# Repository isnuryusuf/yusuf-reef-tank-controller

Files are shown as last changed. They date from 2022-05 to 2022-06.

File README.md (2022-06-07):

# MrAqua Aquarium Controller

This project was based off the iAqua controller written by Dan Cunningham with new features and updates here.

Controller home screen

## Features

- Water temperature monitoring
  - Allows calibration
  - Automatic shutoff of heater if water exceeds setpoint
- Automatic water top-off 
  - Float switch inputs for tank and reservoir
  - Set maximum run-time with alarm flagged if exceeded
  - using non touch water sensor
- Feeding mode
  - Monitor time since last fed
  - Control outlets during feeding (ie turn off pumps)
- Light control 
  - 6-channel PWM or IR control of e-series LED
  - 4 lighting levels (moonlight, sunrise, mid-morning and full daylight)
- Dosing
  - 8 channels
  - Individual settings for each channel
- 8 power outlet control
  - Manual control or set on/off times
  - Aux outlets can be set to cycle times (ie on 10 minutes every 2 hours)
- Buzzer for allerting

## Hardware

- Arduino Mega
- 320 x 240 LCD
- Arduino Mega TFT Shield (or custom shield below)
- 12V power supply
- 8 channel relay board
- DS18B20 temperature sensor
- Peristaltic pumps
- Float switch
- Submersible 12V pump
- (Optional)PCA9685 breakout board

## Libraries

- [Adafruit PWM Servo Driver](https://github.com/adafruit/Adafruit-PWM-Servo-Driver-Library)
- [Dallas Temperature](https://github.com/milesburton/Arduino-Temperature-Control-Library)
- [Time Library](https://github.com/PaulStoffregen/Time)
- [Arduino IR Remote](https://github.com/z3t0/Arduino-IRremote)
- [DS1307RTC](https://github.com/PaulStoffregen/DS1307RTC)
- [SdFat](https://github.com/greiman/SdFat)
- [TimeAlarms](https://github.com/PaulStoffregen/TimeAlarms)
- [UTFT](http://www.rinkydinkelectronics.com/library.php?id=51)
- [UTFT_SdRaw](https://platformio.org/lib/show/565/UTFT_SdRaw)
- [URTouch](http://www.rinkydinkelectronics.com/library.php?id=92)

## Setup

If you are using an ecoxotic e-series LED set "lightCSP" to true, otherwise set it to false.  If you are using a PCA9685 chip for PWM set boolean "PCA9685Installed" to true.

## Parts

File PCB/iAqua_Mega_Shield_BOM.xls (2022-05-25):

Designator | DK# | part_value | Quantity
IR1 |  | IR Transmitter | 1
U1 |  | Mega 2560 | 1
U2, U3, U4, U5, U6 | 296-26482-5-ND | 74HC541PW | 5
U12, U13 | 296-27172-1-ND | ULN2003ANSR | 2 | ULN2003AN | 6
C8, C13 | 311-1458-1-ND | 1u | 2
C12, C14 | 399-6098-ND | 47u | 2 | ELKO Kapasitor 47UF 50V 47UF/50V |  | 8
Q3 (Ambient Light sensor) | 475-1437-ND | SFH 300-3/4 | 1 | TEMT6000
C7 | 490-1799-1-ND | 2u2 | 1
U8 | 497-7253-1-ND | L7805ACD2T-TR | 1
U10 | 497-14661-1-ND | LDF33DT-TR | 1
U9 | 568-8366-5-ND | PCA9685 | 1
ATO, Fan1, Fan2, FloatSwitch1, FloatSwitch2, J2, Pump1, Pump2, Pump3 | 609-3918-ND | 2Pin Terminal Block | 9
P3, P4 | 609-3926-ND | 10Pin Terminal Block | 2
C1, C2, C3, C4, C5, C6, C9, C11 | 1276-1003-1-ND | 100n | 8
C10 | 1276-1123-1-ND | 330n | 1
B1 | 3001K-ND | 3001 | 1
D1, D7 | B340A-FDICT-ND | B340A-13-F | 2
Q4 | DMN3032LE-13DICT-ND | DMN3032LE-13 | 1
U7 | DS1307Z+T&RCT-ND | DS1307 | 1 | DS1307
U11 | MCP9701AT-E/TTCT-ND | MCP9701AT-E/TT | 1 | MCP9700 |  |  | ds18b20
Q1 | MMBT2222AFSCT-ND | MMBT2222A | 1 | Transistor S8050 NPN 0.5A 40V | 4
Q2 | MMBT2907AFSCT-ND | MMBT2907A | 1 | Transistor PN 4355 PN4355
R9, R10, R20, R22, R32, R33 | P1.0KACT-ND | 1K0 | 6
R1, R11 | P4.7KACT-ND | 4K7 | 2
R21 | P10ACT-ND | 10R0 | 1
R4, R5, R12, R13, R14, R15, R16, R24, R30, R34 | P10KACT-ND | 10K0 | 10
R2, R3, R28, R35, R36, R37, R38, R39, R40 | P100ACT-ND | 100R | 9
R27 | P100KACT-ND | 100K | 1
R23 | P499CCT-ND | 499R | 1 | Vishay Dale Resistor 499 Ohm RN60 Series | 6
JP1 | S1011EC-03-ND | 3pin header | 1
P1, P2 | S1011EC-03-ND | 3pin header | 2
P10 (Pin Header Connector) | S1011EC-10-ND | 10Pin Header | 1
HD1, HS1, HS2 (Pin Header Connector) | S2012EC-18-ND, A113648-ND | 38 pin header, 40 pin single row header | 3
P9 (Board Mount Connectors) | S6104-ND | PRPC020DAAN-RC | 1
Y1 | X1123-ND | ECS-3X8X | 1

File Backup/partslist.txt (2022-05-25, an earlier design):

Partlist

Exported from iAqua shield.brd at 12/9/2014 10:39:06 PM

EAGLE Version 6.4.0 Copyright (c) 1988-2013 CadSoft

Assembly variant: 

Part     Value            Package                   Library                    Position (mm)         Orientation

BAT1     3.3V             BATTCON_12MM              SparkFun-Electromechanical (41.46401875 44.49636875) MR90
C1       470pf            C1206                     resistor                   (81.0571875 12.8081)  R0
C2       10uf             C1206                     resistor                   (15.01819375 56.92936875) R0
C3       10uf             C1206                     resistor                   (13.620215625 44.933665625) R270
C4       10uf             C1206                     resistor                   (13.5467375 32.13441875) R270
D1       CGRM4007-G       SOD-123_MINI-SMA          diode                      (32.084071875 75.29981875) R270
D2       CGRM4007-G       SOD-123_MINI-SMA          diode                      (37.9979125 75.186)   R270
D3       CGRM4007-G       SOD-123_MINI-SMA          diode                      (44.097415625 75.182) R270
D4       CGRM4007-G       SOD-123_MINI-SMA          diode                      (50.159846875 75.18935625) R270
D5       CGRM4001-G       SOD-123_MINI-SMA          diode                      (13.080740625 80.4300125) R0
D6       CGRM4001-G       SOD-123_MINI-SMA          diode                      (20.58725 80.4871)    R0
D7       CGRM4001-G       SOD-123_MINI-SMA          diode                      (13.504265625 38.09000625) R270
D8       CGRM4001-G       SOD-123_MINI-SMA          diode                      (13.590159375 52.011784375) R270
IC1      UA7812           TO263-3                   linear                     (22.99915 51.5953875) R270
IC2      UA7805           TO263-3                   linear                     (23.000540625 37.37434375) R270
J1       POWER_JACKPTH    POWER_JACK_PTH            SparkFun-Connectors        (-2.762478125 13.4475875) R270
JP1                       1X01                      pinhead                    (39.3623875 57.384965625) R0
JP2                       1X03                      pinhead                    (85.601328125 5.52231875) R270
JP3                       1X03                      pinhead                    (78.409140625 5.523759375) R90
JP4                       1X04                      pinhead                    (77.156325 78.61265)  R0
JP5                       1X04                      pinhead                    (77.156325 84.2062875) R0
JP6                       1X04                      pinhead                    (77.156321875 89.36450625) R0
JP7                       1X01                      pinhead                    (53.33334375 63.6615375) R0
JP8                       1X01                      pinhead                    (45.70205 63.591934375) R0
JP9                       1X01                      pinhead                    (48.282596875 63.629696875) R0
JP10                      1X01                      pinhead                    (50.815209375 63.653721875) R0
JP11                      1X01                      pinhead                    (18.78530625 62.82380625) R0
JP12                      1X01                      pinhead                    (68.593115625 27.40033125) R0
JP13                      1X01                      pinhead                    (71.142221875 27.383353125) R0
JP14                      1X01                      pinhead                    (78.746009375 27.377815625) R0
JP15                      1X01                      pinhead                    (81.2744375 27.447925) R0
JP16                      1X01                      pinhead                    (73.63146875 27.3715375) R0
JP17                      1X01                      pinhead                    (76.219753125 27.400315625) R0
JP18                      1X01                      pinhead                    (21.316075 62.807553125) R0
LED1     POWER            CHIPLED_1206              led                        (20.334503125 15.73700625) R90
LED2                      LED5MM                    led                        (63.55200625 86.103553125) R180
R1       10K              M1206                     resistor                   (26.472746875 15.75471875) R180
R2       220              M1206                     resistor                   (29.1469 75.711715625) R270
R3       220              M1206                     resistor                   (35.061815625 75.5995625) R270
R4       220              M1206                     resistor                   (41.0167875 75.569996875) R270
R5       220              M1206                     resistor                   (47.19305625 75.58815625) R270
R6       1.8k             M1206                     resistor                   (85.354040625 78.572078125) R180
R7       1.8k             M1206                     resistor                   (85.35463125 84.1430375) R180
R8       220              M1206                     resistor                   (35.9079125 15.438390625) R90
R9       220              M1206                     resistor                   (39.726771875 15.395709375) R90
R10      220              M1206                     resistor                   (43.87718125 15.39609375) R90
R11      220              M1206                     resistor                   (47.6961 15.31066875) R90
R12      220              M1206                     resistor                   (51.847303125 15.310803125) R90
R13      220              M1206                     resistor                   (55.6509875 15.30815) R90
R14      220              M1206                     resistor                   (59.868953125 15.4823) R90
R15      220              M1206                     resistor                   (63.68051875 15.481846875) R90
R31      1K               M1206                     resistor                   (39.126421875 62.447896875) R180
R32      150              M1206                     resistor                   (66.69430625 75.082121875) R180
R33      PHOTOCELLPTH     PHOTOCELL                 SparkFun-Sensors           (71.4802125 8.792246875) R0
R34      100              M1206                     resistor                   (64.80325625 31.58103125) R0
R35      4.7K             M1206                     resistor                   (87.353559375 19.868003125) R180
R36      1K               M1206                     resistor                   (13.55525 75.823171875) R90
R37      1K               M1206                     resistor                   (20.62185 75.475753125) R90
T1                        SOT23-BEC                 transistor                 (45.206290625 58.941078125) R270
T2                        SOT23-BEC                 transistor                 (16.91803125 78.301253125) R0
T3                        SOT23-BEC                 transistor                 (23.96439375 77.9447) R0
U$1      DS1307SO8        SO08                      SparkFun-FreqCtrl          (52.6867 44.71811875) R0
U$2                       1.4CMX1.2CM_HEAT_SINK_PAD Custom Heat Sink           (26.99420625 51.587453125) R0
U$3                       1.4CMX1.2CM_HEAT_SINK_PAD Custom Heat Sink           (26.990246875 37.4647625) R0
U1       ARDUINO-MEGAFULL ARDUINO_MEGA              SparkFun-Boards            (-10.16 17.78)        R0
X1       MKDS1/4-3,81     4POL381                   con-phoenix-381            (45.24549375 86.22636875) R180
X2       MKDS1/2-3,81     2POL381                   con-phoenix-381            (31.799553125 8.8005375) R180
X3       MKDS1/4-3,81     4POL381                   con-phoenix-381            (12.140515625 86.1544375) R0
X4       MKDS1/2-3,81     2POL381                   con-phoenix-381            (39.726053125 8.7846875) R180
X5       MKDS1/2-3,81     2POL381                   con-phoenix-381            (47.69358125 8.7846875) R180
X6       MKDS1/2-3,81     2POL381                   con-phoenix-381            (55.661109375 8.7846875) R180
X7       MKDS1/2-3,81     2POL381                   con-phoenix-381            (63.68655625 8.7846875) R180
X8       MKDS1/2-3,81     2POL381                   con-phoenix-381            (53.097559375 86.224359375) R180
Y1       32.768KHz        TC26H                     SparkFun-FreqCtrl          (51.70250625 38.49364375) R180

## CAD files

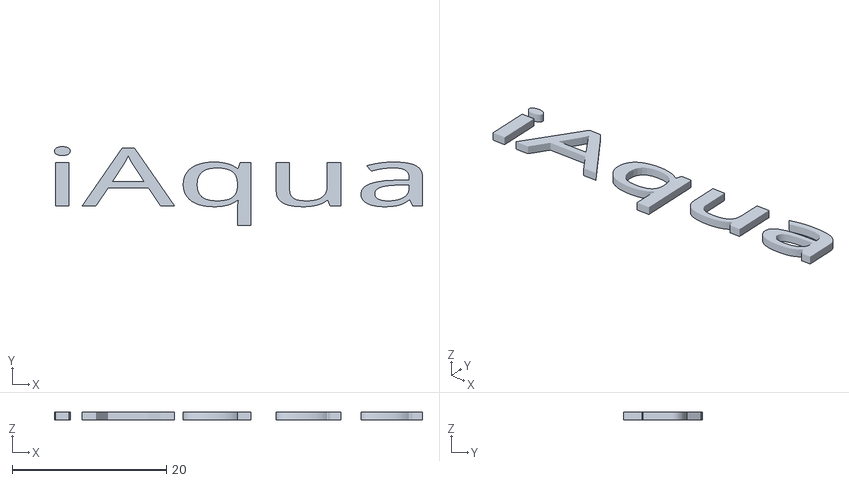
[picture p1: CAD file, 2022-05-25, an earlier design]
Backup/Schrift.stl
47.7 x 10.2 x 1.00

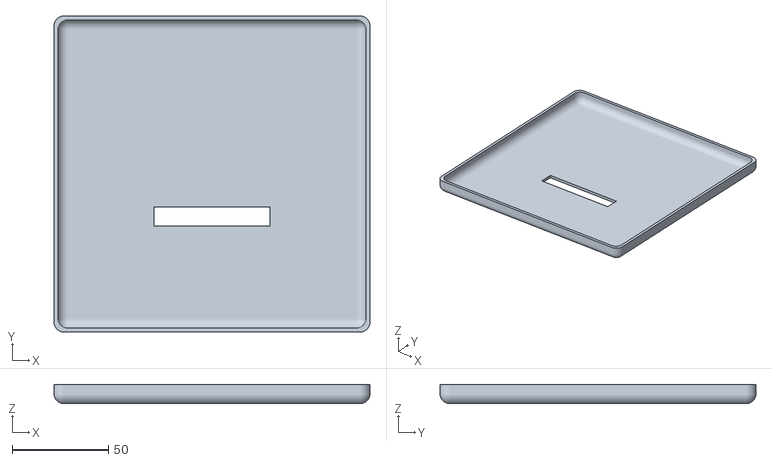
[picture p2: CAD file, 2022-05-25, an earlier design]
Backup/Deckel.stl
164.0 x 164.0 x 10.00

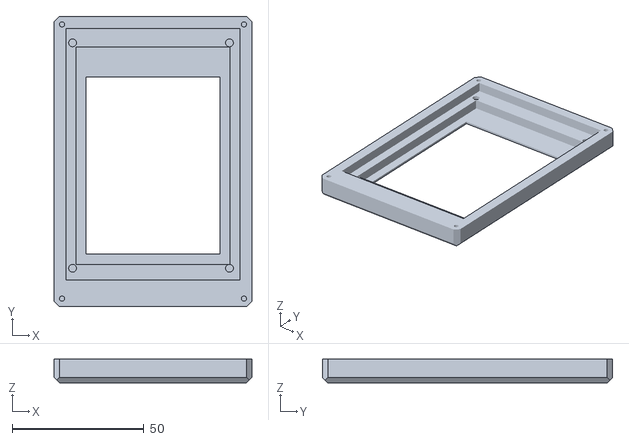
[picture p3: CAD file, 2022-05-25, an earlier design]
Backup/TFT_cover.stl
75.0 x 110.0 x 9.00

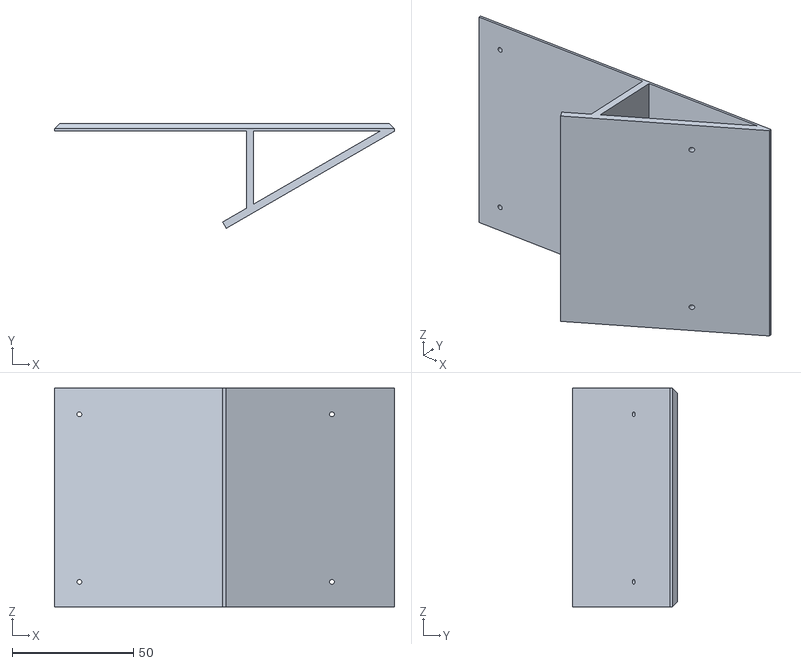
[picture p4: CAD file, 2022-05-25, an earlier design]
Backup/Staender.stl
140.0 x 43.1 x 90.0

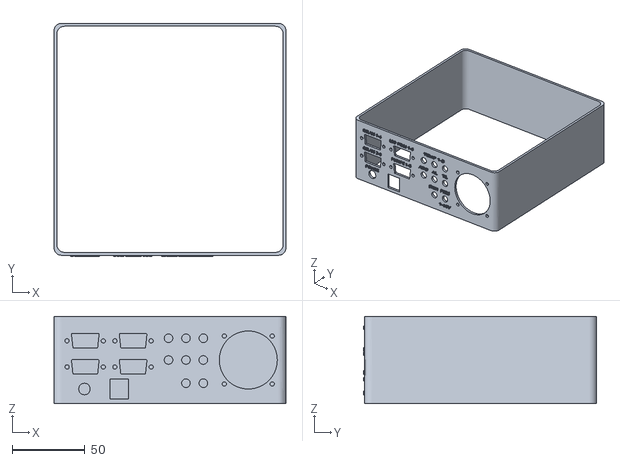
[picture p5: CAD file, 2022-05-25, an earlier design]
Backup/Mittelteil.stl
160.0 x 161.0 x 60.0

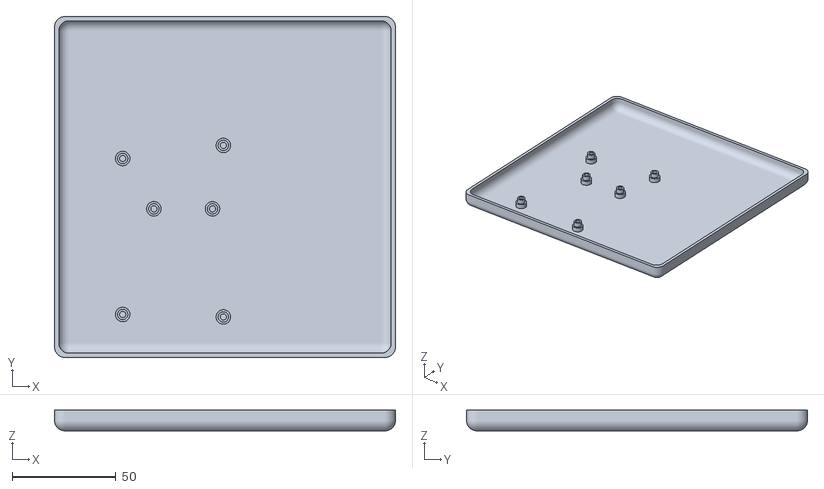
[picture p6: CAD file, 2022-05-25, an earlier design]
Backup/Unterteil.stl
164.0 x 164.0 x 10.00

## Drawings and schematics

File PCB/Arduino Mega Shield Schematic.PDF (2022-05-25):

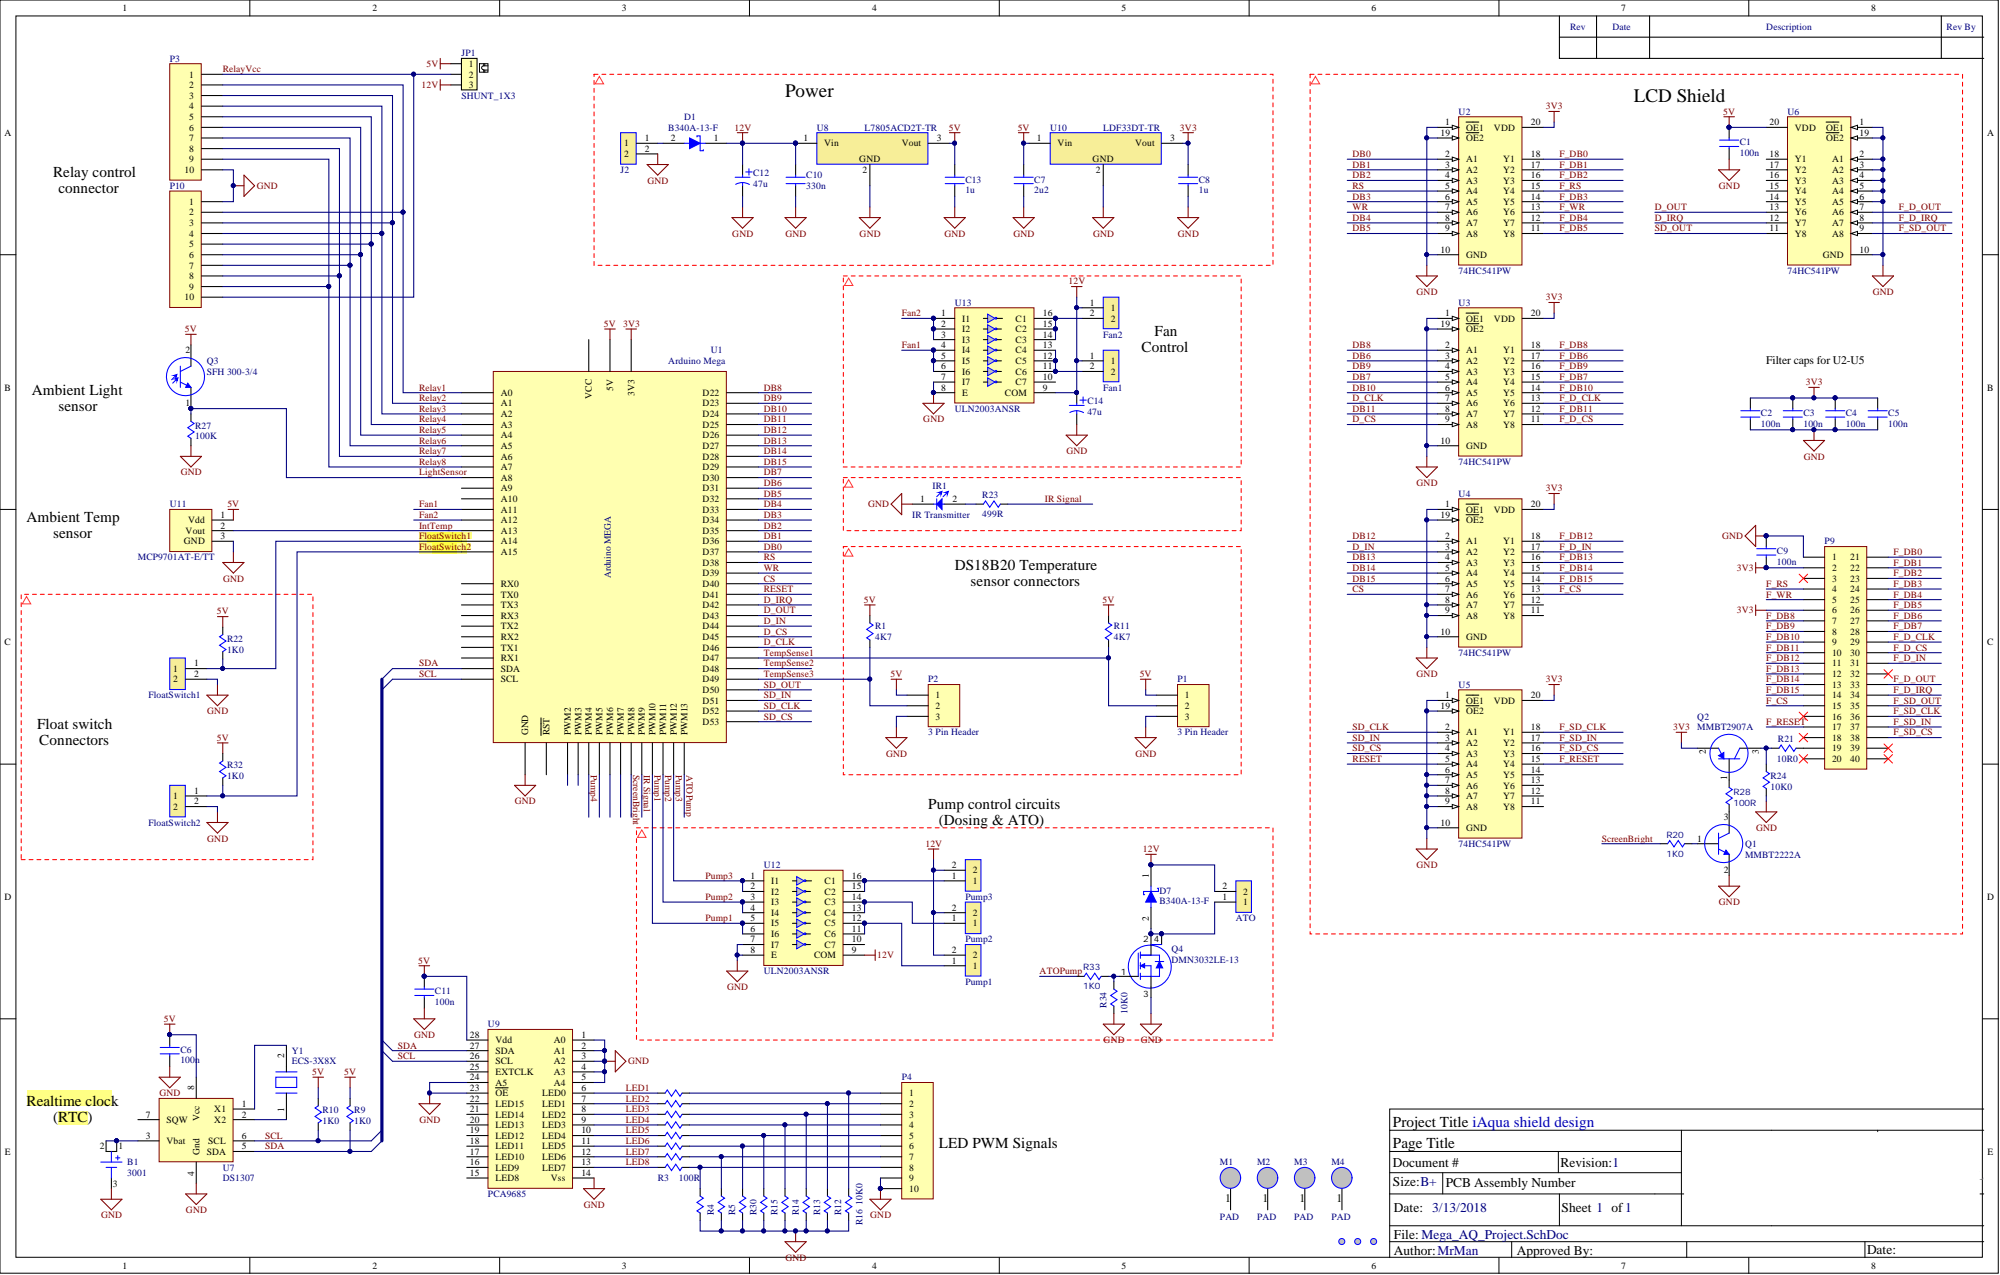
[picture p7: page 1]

2 | D R3 2 | SCL

Page Title | Del ta-Q Technologies Corp. 3755 Wi l l ingdon Bri t ish Columbi | Ave Burnaby a Canada, V5G 3H3 | CO NFIDENTIA PROPRIETARY

# | Revision: 1
B+ | PCB Assembly Number
Date: 3/13/2018 | Sheet 1 of 1 | The information contained in this dr awing is the sole prope rty of Delta -Q T e chnologie s Corp. Any r eproduction in whole or in pa rt without the written pe rmis sion of Delta -Q T e chnologie s Corp. is prohibite d

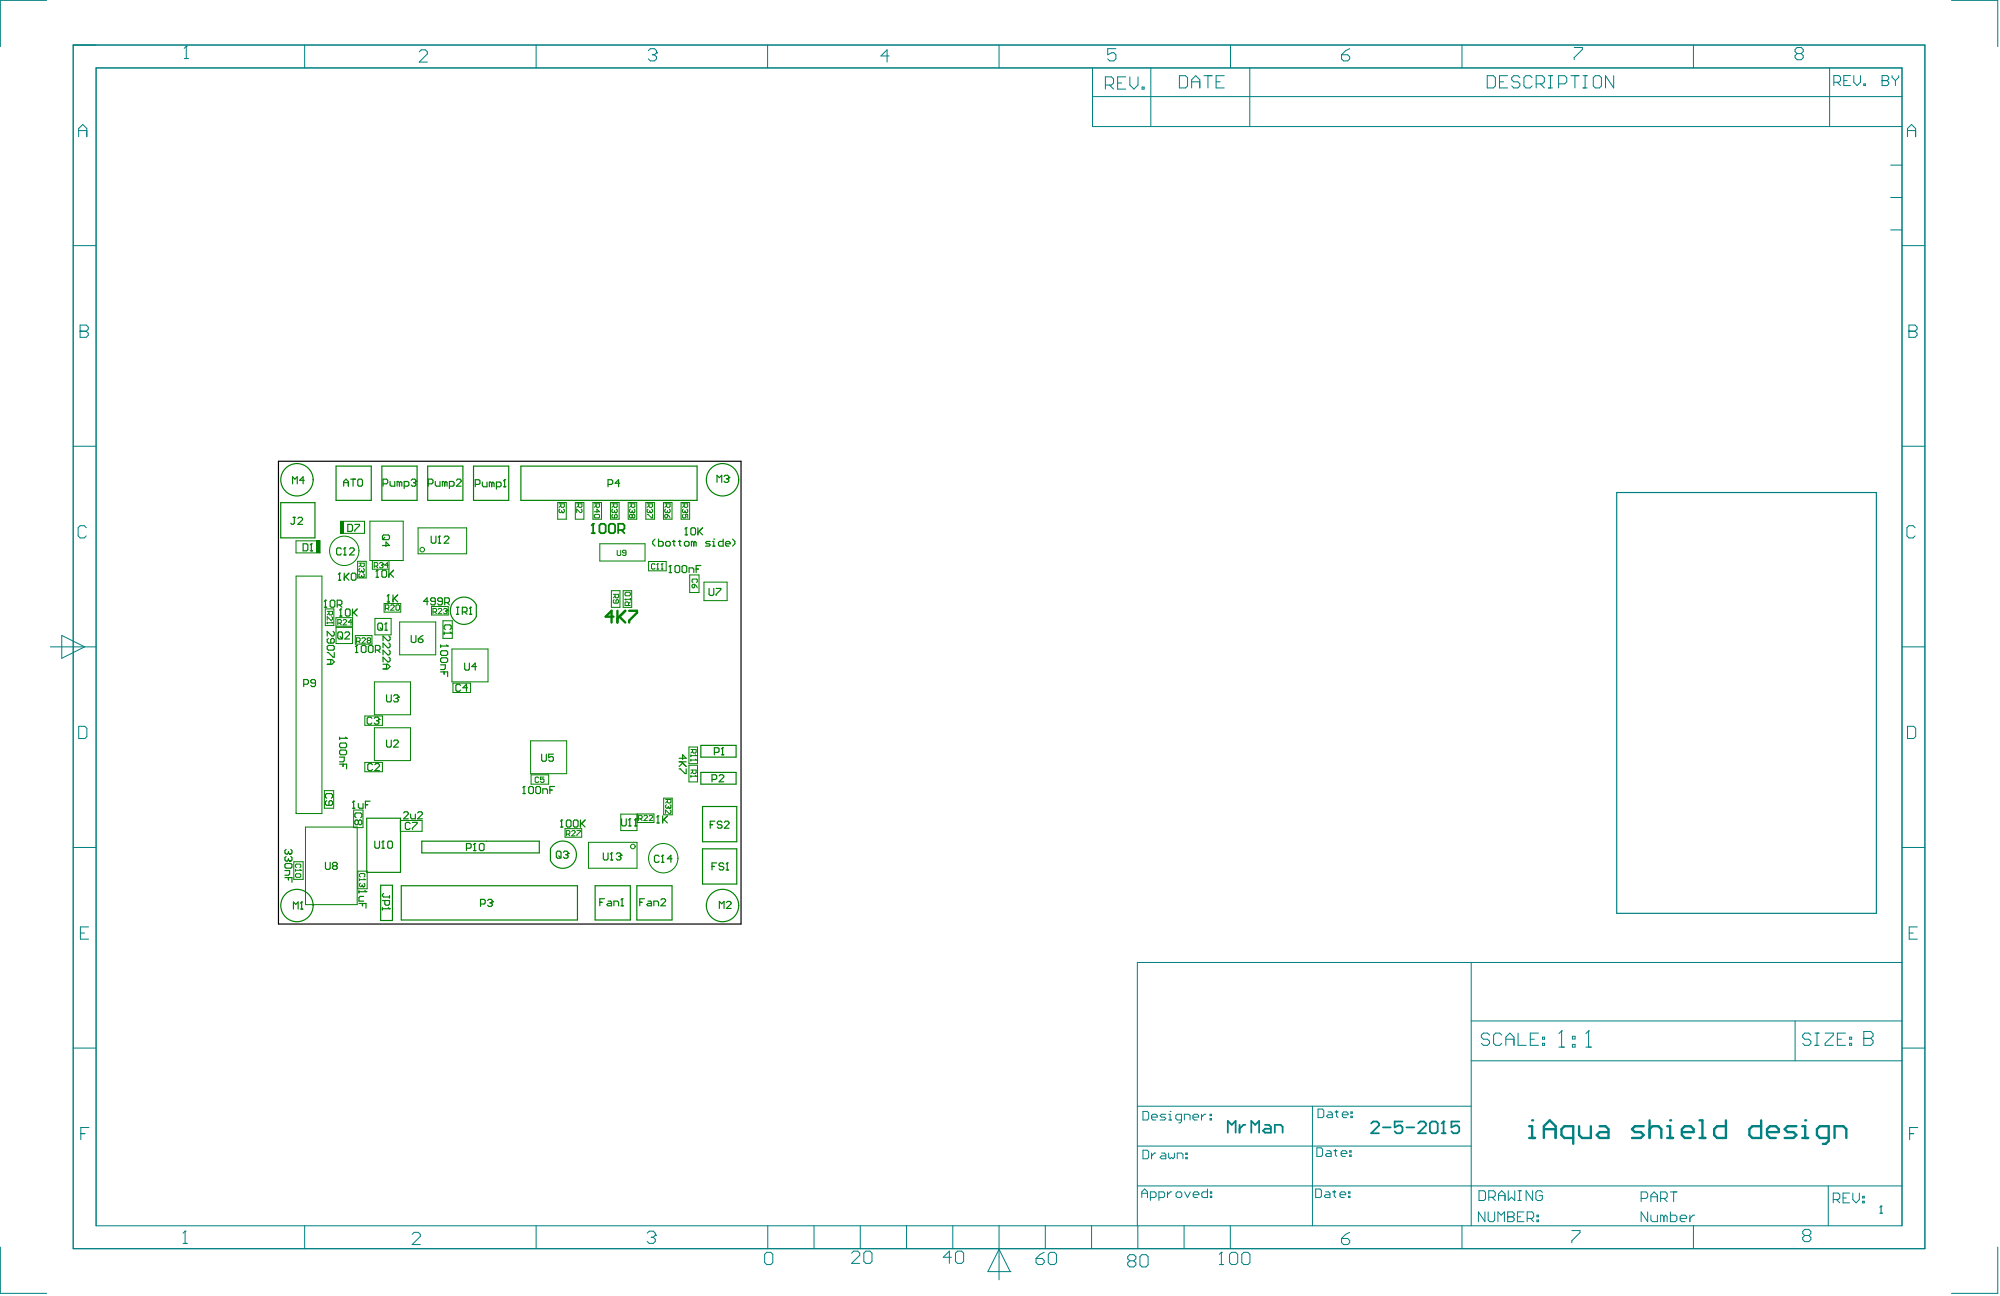
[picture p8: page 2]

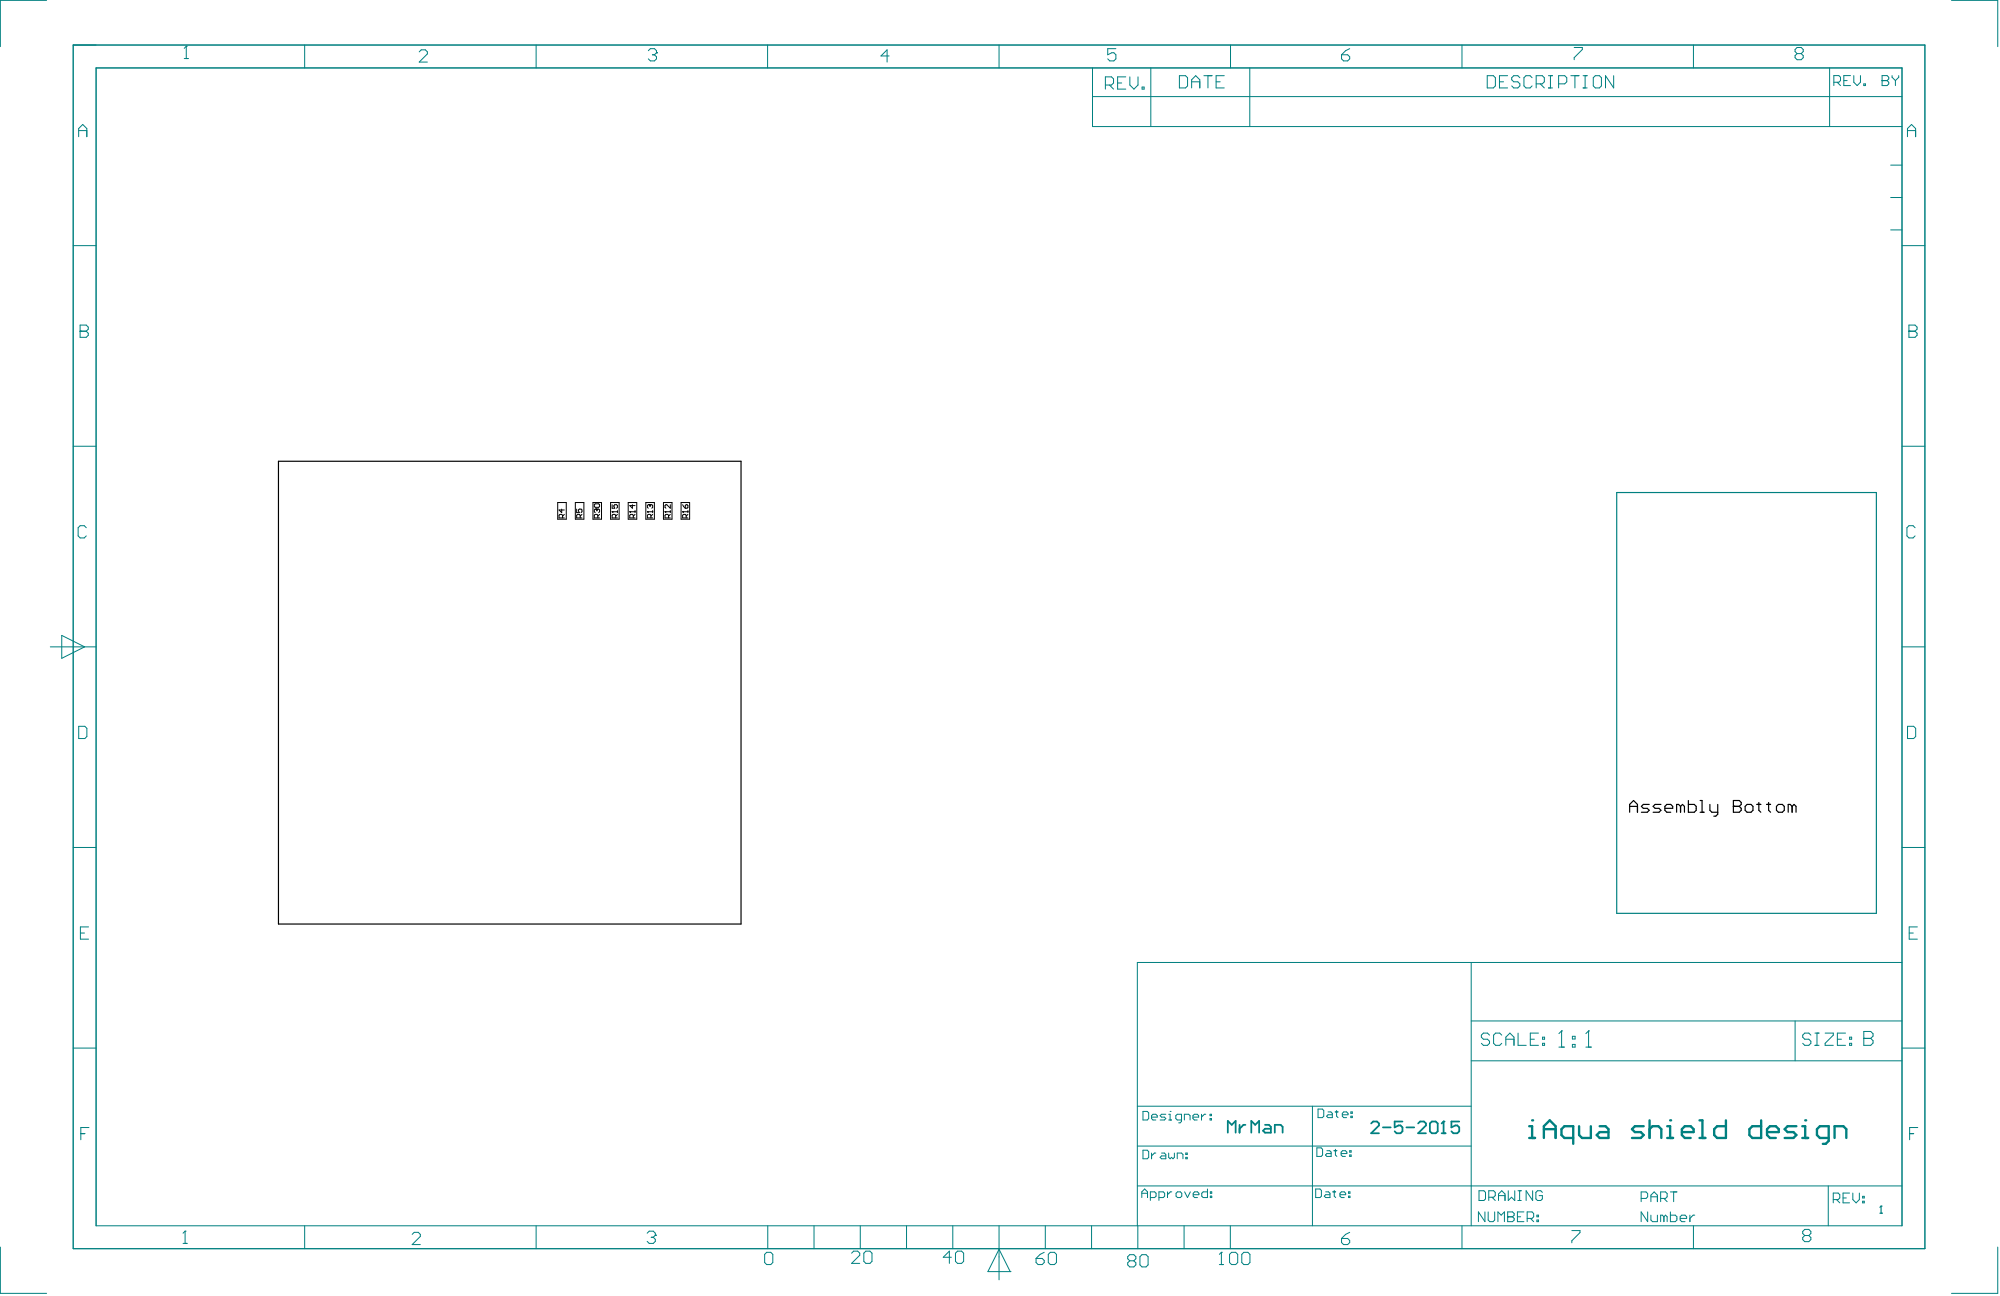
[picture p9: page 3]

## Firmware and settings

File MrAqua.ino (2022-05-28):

// Written by Dan Cunningham, aka AnotherHobby @ plantedtank.net
// Various updates added by Ryan Truss, aka MrMan
// Much code was swiped, modified, and integrated or otherwise inspired from other public works
// All code is public domain, feel free to use, abuse, edit, and share
// Written for Arduino Mega 2560
//
// MrAqua v2.5.3
// -Fixed feeding restart button to only re-start timer
// -Updated screen setting menu to update brightness as it's changed rather than waiting till it
//  dims and then goes bright at a touch
//
// MrAqua v2.5.2
// -Updated feeding to allow not including outlets in feeding routine
// -Updated homescreen ATO display (empty reservoir shows as alarm instead of always displaying)
//
// MrAqua v2.5.0
// -Added watchdog to reset MCU on code freezing
// -Fixed bug where aux1 in timer mode would turn off aux2
// -Updated feeding screen/home screen to show exact time remaining instead of <x minutes
// -Swapped CO2 and Heater pin/icon locations, search for "swapped" to find all instaces and revert
// -Added code to use Serial2 to send/receive information from remote LED module (send LED values, 
//  fan state, reading LED heatsink temperature and request for LED values)
//
// MrAqua v2.4.0
// -Fix power schedule screen (45 degree text is unreadable)
// -Update auto-dimming to use an idle after x minutes timer instead of reading ambient light
// -Home screen now shows all 3 temperatures at the same time if more than just water sensor is enabled
//
// MrAqua v2.3.6
// -Add ability for Aux1 and Aux2 to be used as repeated timer rather than single 24Hr schedule
// -Updated some of the check boxes to on/off icon to fit with theme of the program
// -Updated power alarm behaviours during feeding to avoid devices turning on/off when they shouldn't
//
// MrAqua v2.3.5
// -Fixed startup where outputs would be ON but display showing them OFF
// -Added manual ATO turn-on by pressing section on home screen (runs for max run time)
//
// MrAqua v2.3.3 / 2.3.4
// -Fixed some bugs including heatsink temp sensor using wrong pin, dosing amount limits and PCB temp 
//  sensor not able to read in degrees F
//
// MrAqua v2.3.2
// -Added seperate screen function for IR lights using up/down arrows
// -Dosing alarms now trigger the start but main loop turns them off.  This way the program doesn't
//  freeze when it starts to dose
// -Corrected heatsink temp sensor to use correct device address
//
// MrAqua v2.3.1
// -Added code from alphabeta to add a second on/off schedule for lights
// -Updated light values/system so stored values are always 0-100
// -Updated home screen dosing to correctly draw tubes and not allow remaining volume to go below 0
//
// MrAqua 
// -Updated feeding routine to only toggle filter/pump/aux outputs
// -Added graph display for LED channels 
// -Added routine writeToLED(channel,value) to handle writing to either PCA or Mega PWM pins
// -Modified LED PWM code to optionally use PCA9685 for 12-bit dimming
// -Added 5th/6th LED channel, moved EEPROM for LED values to 400's
// -Added lunar cycle control
// -Added probe settings menu to enable/disable temp sensors and change display units between C and F
// -Added sub-settings menus for sensors to control when fans turn on/off (external fan 
//  controlled by heatsink sensor, internal fan controlled by internal temp) or heater in case of
//  probe 1.  Also added calibration offset for probes
// -Changed feeding, update time and screen dim tracking to using RTC instead of millis 
//  (millis only used for tracking touch timing for better resolution)
// -Changed code for 3 pumps, reworked schedule and setting screens to select a pump and then
//  individual pump dose amounts
// -Added code for ATO
// -Changed LED color setting to bargraph (0-100%) instead of up/down button
// -Added color setting menu for changing bargraph colors
// -Added routine for sending commands to sat+ with the updated bargraphs
// -switched RTClib to DS1307RTC library
// -switched to sdfat and utft_sdraw library for accessing SD card files (can use larger SD 
//  cards and has faster loading speeds)
// -Added read of displayInCelcius to startup
//
// Original iAqua revision documentation:
// CURRENT VERSION 1.0.4
// - the smart startup routine has been reworked and fixed by robsworld78 at The Planted Tank forums!
// - added a first run routine that will zero out all EEPROM data that is needed by iAqua
//
// VERSION 1.0.3
// - fixed smartstartup routine bugs
// - fixed dosing display when resevoir goes negative due to forgettig to hit fill
// - added robsworld78 at The Planted Tank's PWM smart startup lighting code
// - fixed issue when temp turned red, and then turned feeding time red
//
// VERSION:  1.0.2
// - more accurate math for how doses were calcualted on home screen
// - updated power schedules to update home screen immediately
// - day name was off using new RTC and Time library
//
// VERSION:  1.0.1
// - created smart startup routine
// - fixed math bug with dosing pump speed saving to eeprom
// - changed PWM pins for dosing pumps to make room for RGBW PWM pins
// - changed from previous RTC library to RTClib.h
//
// VERSION:  1.0
// - initial version
//
// EEPROM locations (saved settings)
// SPACE // DESCRIPTION
// 0 // 
// 1 // feeding enable filter
// 2 // feeding enable circ
// 3 // feeding enable heat
// 4 // feeding enable co2
// 5 // feeding enable aux 1
// 6 // feeding enable aux 2
// 7 // feeding minutes setting
// 8 // feeding  light 1 (0 off, 1 on)
// 9 // feeding pwr light 2 (0 off, 1 on)
// 10 // feeding pwr filter (0 off, 1 on)
// 11 // feeding pwr circ (0 off, 1 on)
// 12 // feeding pwr heat (0 off, 1 on)
// 13 // feeding pwr co2 (0 off, 1 on)
// 14 // feeding pwr aux 1 (0 off, 1 on)
// 15 // feeding pwr aux 2 (0 off, 1 on)
// 16 // NOT USED
// 17 // heater off temp
// 18 // heater on temp
// 19 // NOT USED
// 20 // pump 1 dose in mL
// 21 // pump 2 dose in mL
// 22 // pump 3 dose in mL
// 23 // pump 1 sec/ml
// 24 // pump 2 sec/ml
// 25 // pump 3 sec/ml
// 26 // dosing reseviors capacity in mL
// 27 // 
// 28 // screen:  return home
// 29 // screen:  autodim level
// 30 // screen:  autodim seconds
// 31 // screen:  brightness if no dim
// 32 // pump 1 remaining volume high byte ^10th
// 33 // pump 1 remaining volume low byte
// 34 // pump 2 remaining volume high byte ^10th
// 35 // pump 2 remaining volume low byte
// 36 // pump 3 remaining volume high byte ^10th
// 37 // pump 3 remaining volume low byte
// ... //
// 40 // ATO Enabled
// 41 // Reservoir switch Enabled
// 42 // Low level wait time in minutes
// 43 // Max run-time / 10
// 44 // ATO alarm flagged
// ... //
// 50 // Temp sensor 1 installed (water)
// 51 // Temp sensor 2 installed (heatsink)
// 52 // Internal sensor installed (MCP9701)
// 53 // Heatsink fan on temperature
// 54 // Heatsink fan off temperature
// 55 // Internal fan on temperature
// 56 // Internal fan off temperature
// 57 // Display in celcius?
// 58 // sensor 1 calibration offset
// 59 // sensor 2 calibration offset
// 60 // sensor 3 calibration offset
// 61 // display sensor 1 on home screen
// 62 // display sensor 2 on home screen
// 63 // display sensor 3 on home screen
// ... // 
// 70 // Lunar cycle enabled
// 71 // Clouds enabled
// 72 // Cloud start hour
// 73 // Cloud start minute
// 74 // Cloud run hours
// 75 // Cloud run minutes
// 76 // Cloud channels enabled (bit 0 = chan1, bit 1 = chan2...)
// ... //
// 80 // bar 1 color
// 81 // bar 2 color
// 82 // bar 3 color
// 83 // bar 4 color
// 84 // bar 5 color
// 85 // bar 6 color
// 86 // bar 7 color
// 87 // bar 8 color
// 88 // bar 9 color
// ... //
// 100-139 // power scheudle
// 220-243 // light ramp schedule
// 280-284 // light bar colors
// 300 // pump1 onHour
// 301 // pump1 onMin
// 302 // pump1 SUN
// 303 // pump1 MON
// 304 // pump1 TUE
// 305 // pump1 WED
// 306 // pump1 THUR
// 307 // pump1 FRI
// 308 // pump1 SAT
// 309-317 // pump2
// 318-326 // pump3
// 327-335 // pump4
// 336-344 // pump5
// 345-353 // pump6
// 354-362 // pump7
// 363-371 // pump8
// ... //
// 400+ // LED values

#include <avr/wdt.h> //added for WDT
#include <Wire.h> // needed by tons of stuff
#include <EEPROM.h>  // used to store and retrieve settings from memory
#include <UTFT.h>  // used to interface with the TFT display
#include <SdFat.h>
#include <UTFT_SdRaw.h>
#include <URTouch.h>  // used to interface with the touch controller on the TFT display
//#include <UTouch.h> //yusuf
#include <DS1307RTC.h>
//#include <DS3232RTC.h> 
//#include <DS3231.h> //yusuf
#include <TimeLib.h>
#include <TimeAlarms.h>  // used to power schedules
#include <IRremote.h>  // used to send IR commands to the light, LED must be on pin 9
#include <OneWire.h> // network library to communicate with the DallasTemperature sensor, 
#include <DallasTemperature.h>  // library for the Temp sensor itself
#include <Adafruit_PWMServoDriver.h> //PCA9865

//yusuf
#include <NewTone.h>
#define TONE_PIN A10 // Pin you have speaker/piezo connected to (be sure to include a 100 ohm resistor).
//#include <SoftwareSerial.h> 
////SoftwareSerial module_bluetooth(0, 1); // pin RX | TX
//SoftwareSerial HM10(0, 1); // RX = 0, TX = 1
//yusuf

UTFT myGLCD(ILI9341_16,38,39,40,41); // start up an instance of the TFT screen
URTouch myTouch(46,45,44,43,42);  // start up an instance of for touch
//UTouch myTouch(46,45,44,43,42); //yusuf
//URTouch myTouch(6, 5, 4, 3, 2); // For standard TFT shield
//UTouch myTouch(6, 5, 4, 3, 2); // yusuf

// file system object
SdFat sd;
const byte ChipSelect = 53; // For TFT Shield
UTFT_SdRaw myFiles(&myGLCD);

// Declare which fonts we will be using
extern uint8_t Sinclair_S[];
extern uint8_t arial_bold[];

//initialize PCA9865
Adafruit_PWMServoDriver pwm = Adafruit_PWMServoDriver(0x40);
Adafruit_PWMServoDriver pwm2 = Adafruit_PWMServoDriver(0x41);

// define relay pins
const int pwrLight1Pin = A0; //arduino A0
const int pwrLight2Pin = A1; //arduino A1
const int pwrFilterPin = A2; //arduino A2
const int pwrCircPin = A3; //arduino A3
//const int pwrHeatPin = A4;  //normal operation
//const int pwrCO2Pin = A5;   //normal operation
const int pwrHeatPin = A5;//co2/heater pins swapped
const int pwrCO2Pin = A4; //co2/heater pins swapped
const int pwrAux1Pin = A6;
const int pwrAux2Pin = A7;

//define misc pins
const int lightSensorPin = A8;  // analog pin for the ambient light sensor
const int pressureSensorPin = A9;  // analog pin for the CO2 pressure sensor

// const int free10Pin = A10;  // last free analog pin
//yusuf
//const int buzzer1Pin = A10; //buzzer to arduino pin analog 10

const int fan1Pin = A11;
const int fan2Pin = A12;

//yusuf change from MCP9701AT-E/TT to DS18B20 
const int internalTempPin = A13;
const int ATOFloatPin = A14;
const int TankFloatPin = A15;
const int thresholdFloat = 10;
const int screenBrightPin = 8; // pwm pin for the LCD backlight
// const int ShouldBeIrSignal = 9; //untuk IR Signal
//define pump pins
const int dosingPump1 = 10;
const int dosingPump2 = 11;
const int dosingPump3 = 12;

//yusuf
const int dosingPump4 = 2; //led1Pin
const int dosingPump5 = 3; //led2Pin
const int dosingPump6 = 4; //led3Pin
const int dosingPump7 = 5; //led4Pin
const int dosingPump8 = 6; //led5Pin
//yusuf

const int ATOPumpPin = 13;
// define RGBW PWM pins
const int led1Pin = 2;
const int led2Pin = 3;
const int led3Pin = 4;
const int led4Pin = 5;
const int led5Pin = 6;
const int led6Pin = 7;

// Pins for temperature sensor
#define ONE_WIRE_BUS_W 47  //water sensor on pin 47 
// Pin 48 for watchdog - see: watchdogSetup
#define ONE_WIRE_BUS_H 49  //Heatsink sensor on pin 49

//yusuf change from MCP9701AT-E/TT to DS18B20 
//#define ONE_WIRE_BUS_I A13  //Internal sensor on pin A13

// Setup a oneWire instance to communicate with any OneWire devices
OneWire oneWireW(ONE_WIRE_BUS_W);
OneWire oneWireH(ONE_WIRE_BUS_H);

//yusuf change from MCP9701AT-E/TT to DS18B20 
//OneWire oneWireI(ONE_WIRE_BUS_I);

// Pass our oneWire reference to Dallas Temperature. 
DallasTemperature sensorW(&oneWireW);
DallasTemperature sensorH(&oneWireH);

//yusuf change from MCP9701AT-E/TT to DS18B20 
//DallasTemperature sensorI(&oneWireI);

// Device address variables
DeviceAddress waterSensor;
DeviceAddress heatsinkSensor;

//yusuf //yusuf change from MCP9701AT-E/TT to DS18B20 
//DeviceAddress internalSensor;

// create an IR instance
IRsend irsend;

byte dispScreen=0;    // screens are listed below
//1-home
//    2-feeding
//    3-power
//    4-settings
//        5 - Light Settings
//        6 - clock
//        7 - feed settings
//        18- sensor settings
//            8 - heater settings
//            19- heatsink fan settings
//            20- internal fan settings
//        9 - Schedule
//            11 - Power schedule
//                12 - Power item
//            15 - Dosing
//            13 - Light ramps schedule screen
//                14 - light ramp schedule
//        10 - Dosing settings (index 1-3 for pump#)
//        16 - Screen settings
//        17 - ATO settings
//        21 - Lunar settings
//        22 - Light bargraph color settings
//        23 - LED graph
//        24 - Light Settings for IR lights

byte scheduleItem; // track which item is being scheduled
byte currentLightMode=0;  //0=high sun, 1=mid sun, 2=low sun, 3=moon, 4=transition, 5=unknown
byte lightEditing=0;  // track if we are actively editing lights

// the next 5 variables will be set at the start of a lighting fade
int fadeDurationSeconds = 0; 
unsigned long fadeStartingSeconds = 0;
unsigned long fadeTimeLeft;
boolean fadeInProgress = false;
byte fadeFromMode = 0;  //0=high sun, 1=mid sun, 2=low sun, 3=moon
byte fadeToMode = 0;  //0=high sun, 1=mid sun, 2=low sun, 3=moon
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
void loop()
{
  unsigned long currentMillis = millis(); // get current millis
  time_t currentTime = now();

  //check temperature every 10 seconds
  if(now() - lastUpdateTime >= 10)
  {
    lastUpdateTime=now();
    checkTemp();
  }
  //check ATO/feeding and update time once per second
  if(now() != lastCheckTime)
  {
    lastCheckTime=now();
    updateTimeDate(false);//passing false results in updating screen only if time or date has changed
    checkATO();
    checkFeeding();
  }
  
  //Check status of current light ramp if applicable
  checkLightRamp();
  
  // check for touch events
  if (myTouch.dataAvailable())
  {
    if (currentMillis - prevMillisTouch > touchWaitTime) // make sure it's been .X sec between touches
    {
      // set backlight touch if not already set and turn up brightness
      if (backlightTouch==false) // backlight touch is for adjusting brightness after touch
      {
        Serial.println(F("Setting backlight to Bright value"));
        backLight = map(screenBrightMem,1,10,10,255);
        analogWrite(screenBrightPin, backLight);
        backlightTouch=true;
      }
      prevMillisTouch=currentMillis; // reset the touch timer
      dimTime = currentTime; // reset screen dim timer
      homeTime = currentTime; // reset return home timer
      processMyTouch();
    }
  }

  // adjust brightness automatically unless touch event
  unsigned long pastSeconds;
  if (screenDimSec!=0) // if set to 0, we won't dim
  {
    if (screenDimLevel!=0) // if set to 0, we won't dim
    {
      if (backlightTouch==true)
      {
        pastSeconds = (currentTime - dimTime);
        if (pastSeconds > screenDimSec)
        {
          Serial.println(F("Reducing backlight to dim level"));
          backlightTouch=false;
          idleBrightness();
        }
      }
    }
  }

  // if we aren't on the home or feeding screen, we return after preset time of no interaction
  if (screenRetHome != 0) // if set to 0, we don't return home
  {
    if ((dispScreen!=1)&&(dispScreen!=2))
    {
      pastSeconds = (currentTime - homeTime);
      if (pastSeconds > (60*screenRetHome)) 
      {
        Serial.println(F("Returning to home"));
        if (dispScreen==9) updateAlarms(); // this will rebuild all of the schedules
        if (dispScreen==5)
        {
          smartStartupRamp();
          setStartupLighting();
        }
        screenHome();
        touchWaitTime = LONG_WAIT;
      }
    }
  }
  
  //Check dosing pumps
  if(pump1State)
  {
    if(currentMillis > pump1StartMillis + pump1millis)
    {
      pump1State = false;
      analogWrite(dosingPump1, 0);
      Serial.print(F("Pump1 done.\n"));
      if(dispScreen == 10)myFiles.load(92, 170, 48, 48, "10test.raw",2);
    }
  }
  if(pump2State)
  {
    if(currentMillis > pump2StartMillis + pump2millis)
    {
      pump2State = false;
      analogWrite(dosingPump2, 0);
      Serial.print(F("Pump2 done.\n"));
      if(dispScreen == 10)myFiles.load(92, 170, 48, 48, "10test.raw",2);
    }
  }
  if(pump3State)
  {
    if(currentMillis > pump3StartMillis + pump3millis)
    {
      pump3State = false;
      analogWrite(dosingPump3, 0);
      Serial.print(F("Pump3 done.\n"));
      if(dispScreen == 10)myFiles.load(92, 170, 48, 48, "10test.raw",2);
    }
  }

  //yusuf
  if(pump4State)
  {
    if(currentMillis > pump4StartMillis + pump4millis)
    {
      pump4State = false;
      analogWrite(dosingPump4, 0);
      Serial.print(F("Pump4 done.\n"));
      if(dispScreen == 10)myFiles.load(92, 170, 48, 48, "10test.raw",2);
    }
  }
  if(pump5State)
  {
    if(currentMillis > pump5StartMillis + pump5millis)
    {
      pump5State = false;
      analogWrite(dosingPump5, 0);
      Serial.print(F("Pump5 done.\n"));
      if(dispScreen == 10)myFiles.load(92, 170, 48, 48, "10test.raw",2);
    }
  }
  if(pump6State)
  {
    if(currentMillis > pump6StartMillis + pump6millis)
    {
      pump6State = false;
      analogWrite(dosingPump6, 0);
      Serial.print(F("Pump6 done.\n"));
      if(dispScreen == 10)myFiles.load(92, 170, 48, 48, "10test.raw",2);
    }
  }
  if(pump7State)
  {
    if(currentMillis > pump7StartMillis + pump7millis)
    {
      pump7State = false;
      analogWrite(dosingPump7, 0);
      Serial.print(F("Pump7 done.\n"));
      if(dispScreen == 10)myFiles.load(92, 170, 48, 48, "10test.raw",2);
    }
  }
  if(pump8State)
  {
    if(currentMillis > pump8StartMillis + pump8millis)
    {
      pump8State = false;
      analogWrite(dosingPump8, 0);
      Serial.print(F("Pump8 done.\n"));
      if(dispScreen == 10)myFiles.load(92, 170, 48, 48, "10test.raw",2);
    }
  }
  //yusuf
  
  //Check aux1/2 timers
  if(aux1TimerState)
  {
    if(currentMillis > (aux1TimerStart + aux1TimerFinish))
    {
      AlarmPwrAux1_Off();
      aux1TimerState = false;
      Serial.println(F("Aux1 timer finished."));
    }
  }
  if(aux2TimerState)
  {
    if(currentMillis > (aux2TimerStart + aux2TimerFinish))
    {
      AlarmPwrAux2_Off();
      aux2TimerState = false;
      Serial.println(F("Aux2 timer finished."));
    }
  }
  
  Alarm.delay(10); // must use Alarm delay to use the TimeAlarms library
  doggieTickle();
  /*
  //Parse command/requests from light fixture (only expect TEMP-XX.XX or 
  //LEDValues request at this point)
  if(Serial2.available())
  {
    //if we have received data read it into input char array
    byte size = Serial2.readBytes(input, INPUT_SIZE);
    input[size] = 0;
    char* separator = strchr(input, '-');
    //Check to see if message is incoming data
    if (separator != 0)
    {
      //Received data, actually split the string in 2, replace '-' with 0 and 
      //increase separator to point at the actual value
      *separator = 0;
      ++separator;
      String command = "";
      command.reserve(10);
      command = input;
      
      Serial.print(F("Parameter received: "));
      Serial.println(command);
      
      //do a case structure based on command
      if(command == "TEMP")
      {
        //received value of heatsink temperature
        temperature2 = atof(separator);
        Serial.print(F("Temperature2: "));
        Serial.println(temperature2);
      }
    }
    //check to see if message is a request
    separator = strchr(input, '?');
    if (separator != 0)
    {
      *separator = 0;
      ++separator;
      String request = "";
      request.reserve(10);
      request = input;
      
      Serial.print(F("Request received: "));
      Serial.println(request);
      
      if(request == "LEDValues")
      {
        //received request for all LED channel values
        Serial.println(F("Sending LED values"));
        writeToLED(1,currentColor.chan1);
        writeToLED(2,currentColor.chan2);
        writeToLED(3,currentColor.chan3);
        writeToLED(4,currentColor.chan4);
        writeToLED(5,currentColor.chan5);
        writeToLED(6,currentColor.chan6);
      }
    }
  }*/
  //End Serial2 monitoring

  //yusuf
  //if(Serial3.available() > 0)  
  //{
  //  data = Serial3.read();Serial3.print(data);    //Pembacaan dan ditampilkan data yang masuk   
  //  Serial3.print("\n"); 
    //Data yang masuk      
  //  if(data == '1'){
  //  digitalWrite(13, HIGH);//diberikan waktu tunda 1 detik
  //  }
  //  else if(data == '0')      
  //  digitalWrite(13, LOW);  
  //}

  //yusuf
  //HM10.listen();  // listen the HM10 port
  //while (HM10.available() > 0) {   // if HM10 sends something then read
  //  appData = HM10.read();
  //  inData = String(appData);  // save the data in string format
  //  Serial3.write(appData);
  //}
  //if (Serial3.available()) {           // Read user input if available.
  //  delay(10);
  //  HM10.write(Serial3.read());
  //}
  //if ( inData == "F") {
  //  Serial3.println("LED OFF");
  //  digitalWrite(13, LOW); // switch OFF LED
  //  delay(500);
  //}
  //if ( inData == "N") {
  //  Serial3.println("LED ON");
  //  digitalWrite(13, HIGH); // switch OFF LED
  //  delay(500);
  //  digitalWrite(13, LOW); // switch OFF LED
  //  delay(500);
  //}   
  //yusuf

}

//yusuf
void buzzerAlert() 
{
  NewTone(TONE_PIN, 1000); // Send 1KHz sound signal...
  delay(1000);        // ...for 1 sec
  noNewTone(TONE_PIN);     // Stop sound...
  delay(3000);        // ...for 1sec
}
//yusuf
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

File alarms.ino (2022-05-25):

void updateAlarms()
{
  // clear, free, delete all possible alarms
  for (byte i=0; i<=50; i++) Alarm.free(i);

  //////// POWER ALARMS ////////
  if (schedLights1.active==1)
  {
    Alarm.alarmRepeat(schedLights1.onHour,schedLights1.onMinute,0,AlarmPwrLight1_On);
    Alarm.alarmRepeat(schedLights1.offHour,schedLights1.offMinute,0,AlarmPwrLight1_Off);
  }
  if (schedLights1s2.active==1)
  {
    Alarm.alarmRepeat(schedLights1s2.onHour,schedLights1s2.onMinute,0,AlarmPwrLight1_On);
    Alarm.alarmRepeat(schedLights1s2.offHour,schedLights1s2.offMinute,0,AlarmPwrLight1_Off);
  }
  if (schedLights2.active==1)
  {
    Alarm.alarmRepeat(schedLights2.onHour,schedLights2.onMinute,0,AlarmPwrLight2_On);
    Alarm.alarmRepeat(schedLights2.offHour,schedLights2.offMinute,0,AlarmPwrLight2_Off);
  }
  if (schedLights2s2.active==1)
  {
    Alarm.alarmRepeat(schedLights2s2.onHour,schedLights2s2.onMinute,0,AlarmPwrLight2_On);
    Alarm.alarmRepeat(schedLights2s2.offHour,schedLights2s2.offMinute,0,AlarmPwrLight2_Off);
  }
  if (schedCirc.active==1)
  {
    Alarm.alarmRepeat(schedCirc.onHour,schedCirc.onMinute,0,AlarmPwrCirc_On);
    Alarm.alarmRepeat(schedCirc.offHour,schedCirc.offMinute,0,AlarmPwrCirc_Off);
  }
  if (schedCo2.active==1)
  {
    Alarm.alarmRepeat(schedCo2.onHour,schedCo2.onMinute,0,AlarmPwrCO2_On);
    Alarm.alarmRepeat(schedCo2.offHour,schedCo2.offMinute,0,AlarmPwrCO2_Off);
  }
  if (schedAux1.active==1)
  {
    if(schedAux1.timer==0)
    {
      Alarm.alarmRepeat(schedAux1.onHour,schedAux1.onMinute,0,AlarmPwrAux1_On);
      Alarm.alarmRepeat(schedAux1.offHour,schedAux1.offMinute,0,AlarmPwrAux1_Off);
    }else
    {
      Alarm.timerRepeat(schedAux1.onHour,schedAux1.onMinute,0,AlarmPwrAux1_Timer);
    }
  }
  if (schedAux2.active==1)
  {
    if(schedAux1.timer==0)
    {
      Alarm.alarmRepeat(schedAux2.onHour,schedAux2.onMinute,0,AlarmPwrAux2_On);
      Alarm.alarmRepeat(schedAux2.offHour,schedAux2.offMinute,0,AlarmPwrAux2_Off);
    }else
    {
      Alarm.timerRepeat(schedAux2.onHour,schedAux2.onMinute,0,AlarmPwrAux2_Timer);
    }
  }

  //////// RAMP ALARMS ////////
  Alarm.alarmRepeat(ramp1.onHour,ramp1.onMinute,0,AlarmRamp1);
  Alarm.alarmRepeat(ramp2.onHour,ramp2.onMinute,0,AlarmRamp2);
  Alarm.alarmRepeat(ramp3.onHour,ramp3.onMinute,0,AlarmRamp3);
  Alarm.alarmRepeat(ramp4.onHour,ramp4.onMinute,0,AlarmRamp4);
  Alarm.alarmRepeat(ramp5.onHour,ramp5.onMinute,0,AlarmRamp5);
  Alarm.alarmRepeat(ramp6.onHour,ramp6.onMinute,0,AlarmRamp6);
  
  //////// Ramp PWM to 0, 4 hours after ramp6 ////////
  byte zeroHour = ((ramp6.onHour + 4) % 24);
  byte zeroMin = ramp6.onMinute;
  Alarm.alarmRepeat(zeroHour,zeroMin,0,rampToZero);
  
  //////// DOSING ALARMS ////////
  if (pump1.Sunday==1)
  {
    Alarm.alarmRepeat(dowSunday, pump1.onHour,pump1.onMinute,0,AlarmMacros);
  }
  if (pump2.Sunday==1)
  {
    Alarm.alarmRepeat(dowSunday, pump2.onHour,pump2.onMinute,0,AlarmMicros);
  }
  if (pump3.Sunday==1)
  {
    Alarm.alarmRepeat(dowSunday, pump3.onHour,pump3.onMinute,0,AlarmExcel);
  }

  //yusuf
  if (pump4.Sunday==1)
  {
    Alarm.alarmRepeat(dowSunday, pump4.onHour,pump4.onMinute,0,AlarmPump4);
  }
  if (pump5.Sunday==1)
  {
    Alarm.alarmRepeat(dowSunday, pump5.onHour,pump5.onMinute,0,AlarmPump5);
  }
  if (pump6.Sunday==1)
  {
    Alarm.alarmRepeat(dowSunday, pump6.onHour,pump6.onMinute,0,AlarmPump6);
  }
  if (pump7.Sunday==1)
  {
    Alarm.alarmRepeat(dowSunday, pump7.onHour,pump7.onMinute,0,AlarmPump7);
  }
  if (pump8.Sunday==1)
  {
    Alarm.alarmRepeat(dowSunday, pump8.onHour,pump8.onMinute,0,AlarmPump8);
  }
  //yusuf
  
  if (pump1.Monday==1)
  {
    Alarm.alarmRepeat(dowMonday, pump1.onHour,pump1.onMinute,0,AlarmMacros);
  }
  if (pump2.Monday==1)
  {
    Alarm.alarmRepeat(dowMonday, pump2.onHour,pump2.onMinute,0,AlarmMicros);
  }
  if (pump3.Monday==1)
  {
    Alarm.alarmRepeat(dowMonday, pump3.onHour,pump3.onMinute,0,AlarmExcel);
  }

  //yusuf
  if (pump4.Monday==1)
  {
    Alarm.alarmRepeat(dowMonday, pump4.onHour,pump4.onMinute,0,AlarmPump4);
  }
  if (pump5.Monday==1)
  {
    Alarm.alarmRepeat(dowMonday, pump5.onHour,pump5.onMinute,0,AlarmPump5);
  }
  if (pump6.Monday==1)
  {
    Alarm.alarmRepeat(dowMonday, pump6.onHour,pump6.onMinute,0,AlarmPump6);
  }
  if (pump7.Monday==1)
  {
    Alarm.alarmRepeat(dowMonday, pump7.onHour,pump7.onMinute,0,AlarmPump7);
  }
  if (pump8.Monday==1)
  {
    Alarm.alarmRepeat(dowMonday, pump8.onHour,pump8.onMinute,0,AlarmPump8);
  }
  //yusuf

  
  if (pump1.Tuesday==1)
  {
    Alarm.alarmRepeat(dowTuesday, pump1.onHour,pump1.onMinute,0,AlarmMacros);
  }
  if (pump2.Tuesday==1)
  {
    Alarm.alarmRepeat(dowTuesday, pump2.onHour,pump2.onMinute,0,AlarmMicros);
  }
  if (pump3.Tuesday==1)
  {
    Alarm.alarmRepeat(dowTuesday, pump3.onHour,pump3.onMinute,0,AlarmExcel);
  }

  //yusuf
  if (pump4.Tuesday==1)
  {
    Alarm.alarmRepeat(dowTuesday, pump4.onHour,pump4.onMinute,0,AlarmPump4);
  }
  if (pump5.Tuesday==1)
  {
    Alarm.alarmRepeat(dowTuesday, pump5.onHour,pump5.onMinute,0,AlarmPump5);
  }
  if (pump6.Tuesday==1)
  {
    Alarm.alarmRepeat(dowTuesday, pump6.onHour,pump6.onMinute,0,AlarmPump6);
  }
  if (pump7.Tuesday==1)
  {
    Alarm.alarmRepeat(dowTuesday, pump7.onHour,pump7.onMinute,0,AlarmPump7);
  }
  if (pump8.Tuesday==1)
  {
    Alarm.alarmRepeat(dowTuesday, pump8.onHour,pump8.onMinute,0,AlarmPump8);
  }
  //yusuf
  
  if (pump1.Wednesday==1)
  {
    Alarm.alarmRepeat(dowWednesday, pump1.onHour,pump1.onMinute,0,AlarmMacros);
  }
  if (pump2.Wednesday==1)
  {
    Alarm.alarmRepeat(dowWednesday, pump2.onHour,pump2.onMinute,0,AlarmMicros);
  }
  if (pump3.Wednesday==1)
  {
    Alarm.alarmRepeat(dowWednesday, pump3.onHour,pump3.onMinute,0,AlarmExcel);
  }

  //yusuf
  if (pump4.Wednesday==1)
  {
    Alarm.alarmRepeat(dowWednesday, pump4.onHour,pump4.onMinute,0,AlarmPump4);
  }
  if (pump5.Wednesday==1)
  {
    Alarm.alarmRepeat(dowWednesday, pump5.onHour,pump5.onMinute,0,AlarmPump5);
  }
  if (pump6.Wednesday==1)
  {
    Alarm.alarmRepeat(dowWednesday, pump6.onHour,pump6.onMinute,0,AlarmPump6);
  }
  if (pump7.Wednesday==1)
  {
    Alarm.alarmRepeat(dowWednesday, pump7.onHour,pump7.onMinute,0,AlarmPump7);
  }
  if (pump8.Wednesday==1)
  {
    Alarm.alarmRepeat(dowWednesday, pump8.onHour,pump8.onMinute,0,AlarmPump8);
  }
  //yusuf
  
  if (pump1.Thursday==1)
  {
    Alarm.alarmRepeat(dowThursday, pump1.onHour,pump1.onMinute,0,AlarmMacros);
  }
  if (pump2.Thursday==1)
  {
    Alarm.alarmRepeat(dowThursday, pump2.onHour,pump2.onMinute,0,AlarmMicros);
  }
  if (pump3.Thursday==1)
  {
    Alarm.alarmRepeat(dowThursday, pump3.onHour,pump3.onMinute,0,AlarmExcel);
  }
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

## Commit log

2022-05-25 initial
    initial
    [Deckel.stl, Mittelteil.stl, Schrift.stl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]
2022-05-26 add 5 more pump
    add 5 more pump
2022-05-26 add buzzer
    add buzzer
    [MrAqua.ino]
2022-05-26 Add non-contact Water Sensor
    Add non-contact Water Sensor
